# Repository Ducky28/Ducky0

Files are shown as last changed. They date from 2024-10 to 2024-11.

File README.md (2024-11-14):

# Ducky0
A Voron 0.2r1 CoreXY 3D Printer Modification

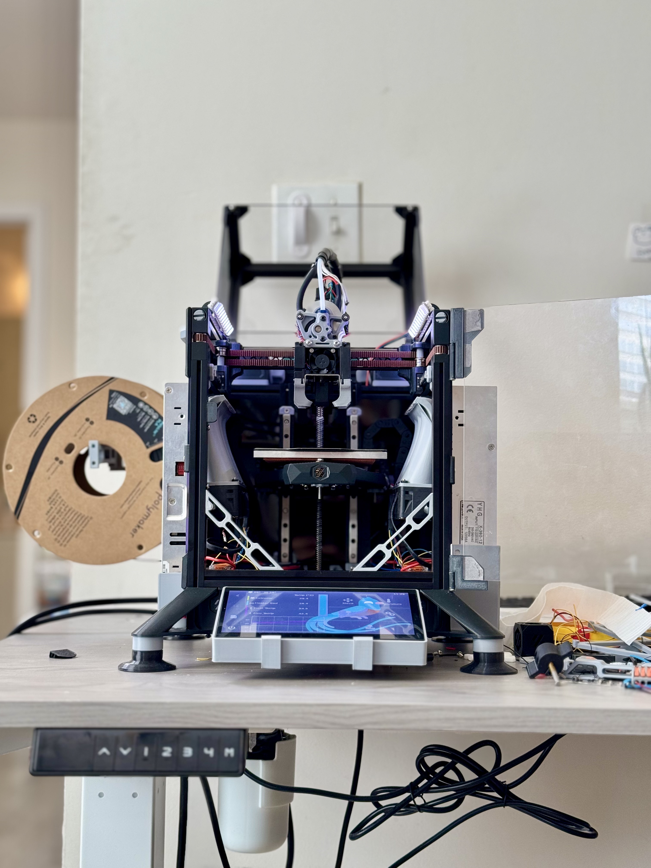
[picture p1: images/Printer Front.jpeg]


## Wait! But Why?
I often find myself in this situation: *sends prototype to 3D printer, 3D printer is done an hour later, realizes I'm on version 7 of the design* 
## Design goals
* Robustness
    * Stiffen up frame where possible
    * Double shear AB motor mounts for higher belt tensions
    * Ultrawide stance feet for added stability
    * Overspecced MCU and Klipper Host to avoid stability issues
* Part cooling
    * 6 4028 Delta fans for sheet cooling
    * 2 4010 blower fans for tool head part cooling
    * Dedicated 12V supply for fans
* Electronics cooling
    * As much cooling as possible for XY and Z motors
    * put heatinks on stepper stators to improve heat transfer to the air
    * Fans for high current and fast switching components (like stepper drivers)
* Extrusion system
    * [Deconstruder tool head](https://github.com/TheRealDeathsneeze/Deconstruder/tree/main)
    * 60-80mm^3/sec volumetric flow rate
    * 0.4mm high flow nozzle
    * Decently high torque extruder
* XYZ motion
    * 100,000mm/sec^2 acceleration
    * 1000mm/sec speed (600-700mm/sec printing speed)
    * Ultra light gantry
    * 5000mm/sec^2 Z acceleration
    * 200mm/sec Z speed
* Power
    * 5V 25W USB-C supply for Raspberry Pi 
    * 12V 350W PSU for fans
    * 24V 350W PSU for main electronics
    * 48V 200W PSU for XY motors
    * Separately switch 48V supply from the rest of the supplies
* Printing Capabilities
  * Fully enclosed with standard tophat and door
  * Fully contained part cooling
  * Copper heatblock for up to 450C
  * Heated bed up to 120C
  * Max observed chamber temperature: 75C

* Must be able to print these materials
     * ABS/ASA
     * PET
     * PA6/PA12
     * PLA
     * PETG
     * PC
   
## Components and Resources
* Frame Components
  * [Voron V0 Frame Brace by Jon](https://www.printables.com/model/450049-voron-v0-frame-brace)
  * [Voron V0 Stealth Handles by Maple Leaf Makers](https://www.printables.com/model/481575-voron-v0-stealth-handles)
  * Extrusions and mounting hardware used in formbot kit
* Tool head and gantry
    * [Deconstruder tool head by Becca Kay](https://github.com/TheRealDeathsneeze/Deconstruder)
    * 4010 12krpm GDSTime fans
    * NF Crazy Copper Volcano High Flow
    * 0.4mm Bondtech Brass CHT nozzle
    * LDO-36STH20-1004AHG(8T) extruder motor
    * PT1000 thermistor
    * 120W heater cartridge
* XY Motion
  * Fysetc Voron 0 ultra light gantry
  * [Double shear AB motor mounts by Driftrotor](https://github.com/Driftrotor/Voron-V0.2r1-Double-Shear-AB-Motor-Mounts/tree/main)
  * LDO-35sth52-2004AH(s35) XY motors
  * 2 3010 fans for stepper cooling
  * 2 3010 blower fans for stepper cooling
  * 2 12032 blower fans for stepper cooling
* Electronics
  * Raspberry pi 4 for Klipper Host
  * BTT SKR 3 for primary Klipper MCU
  * LDO Nitehawk 36 for tool board MCU
  * 2 Mellow Fly TMC5160 Pro drivers for XY motors
  * 2 BTT TMC2209 stepper drivers for Z and E motors
  * 4 4010 fans for electronics cooling
  * Remixed Voron 0.2 printed bottom panel. [original model by Cthulhu](https://www.printables.com/model/467247-voron-02-printed-bottom-panel)
  * [Mellow Fly HV-TMC5160 Pro Driver case by Hundsbuah](https://www.thingiverse.com/thing:5792659)
  * Embedded glass bead thermistors inside AB motors to track motor winding temperature
  * Makerbase MKS 3MOS fan mosfets
* Misc
  * 6 Delta Electronics PFB0412EN-E fans
  * Fysetc CNC bed frame
  * [4028 Air ducts by Coconut](https://github.com/CoconutDevelopment/CocobustorZero/tree/main/STLs/Coconut%20Air%20Ducts)
  * [Superwide Stance feet by Coconut](https://github.com/CoconutDevelopment/CocobustorZero/tree/main/STLs/Superwide%20Stance)
  * BTT Pi TFT70 touchscreen
  * [BTT Pi TFT70 screen enclosure by Fizzy's Tech](https://www.printables.com/model/581227-ft-btt-pi-tft70-screen-mount/files)
  * [Voron 0 Kirigami Bed by christophmuellerorg](https://github.com/christophmuellerorg/voron_0_kirigami_bed)
  * [Rainbow on a Matchstick by Blamm](https://github.com/VoronDesign/Voron-Hardware/tree/master/Daylight/Rainbow_on_a_matchstick)
  * [Lift-Off Tophat Hinges by chirpy2605](https://github.com/chirpy2605/voron/tree/main/V0/Lift-Off_Tophat_Hinges)
  * [Remixed MF Nano carbon filter by kejar31](https://www.printables.com/model/500513-voron-v0-tiny-recirculating-carbon-filter-mfnano-r)

## Short Video
Video (https://www.youtube.com/watch?v=nS1hlO0ZEqE)

## Explainer Video
Video (https://www.youtube.com/watch?v=TwCCUQ7yJMo)

## Benchy!
Video (https://www.youtube.com/watch?v=4r7pd2CCRk0)

## Authors

[@Ducky28](https://github.com/Ducky28)

## Version History

* 0.1.19
     * Added Klipper Expander board for more I/O
     * [Added Remixed MF Nano carbon filter by kejar31](https://www.printables.com/model/500513-voron-v0-tiny-recirculating-carbon-filter-mfnano-r)
     * Added 2 chamber thermistors to monitor chamber temp
     * Separated fan controls for better control over different fans
     * moved pin definitions around to more sensible hardware (no more turning fans on and off with a high power heater mosfet)

* 0.1.01
     * Added Thermistors and thermal adhesive to BOM for embedding thermistors inside motors
     * Added KAMP Smart Park and Adaptive Purge routines in PRINT_START
     * Added Orcaslicer, Prusaslicer, and Cura print profiles for KAMP conditional gcodes
     * Still work in progress, things may still not work as expected!

* 0.1
    * Initial Release
    * Still work in progress, things may not work as expected!
 
## License

This project is licensed under the GPL-V3.0 License - see the LICENSE.md file for details

## Acknowledgments

* [VoronDesign](https://github.com/VoronDesign)
  * [Voron 0.2r1](https://github.com/VoronDesign/Voron-0)
  * [Klipper Expander by Tim Abraham](https://github.com/VoronDesign/Voron-Hardware/tree/master/Klipper_Expander/Documentation)
* [Klipper3D Klipper](https://github.com/Klipper3d/klipper)
  * [Klippain Shaketune by Frix-x](https://github.com/Frix-x/klippain-shaketune)
  * [Klipper TMC Autotune by Andrew McGregor](https://github.com/andrewmcgr/klipper_tmc_autotune)
  * [Klipperscreen by Jordan Ruthe](https://github.com/KlipperScreen/KlipperScreen)
  * [KAMP by kyleisah](https://github.com/kyleisah/Klipper-Adaptive-Meshing-Purging)
* [Coconut](https://github.com/CoconutDevelopment)
  * [CocobustorZero](https://github.com/CoconutDevelopment/CocobustorZero)
* [247 printing's 247 Zero Beta2](https://github.com/247printing/247zero)
* [Stefan's (CNC Kitchen) "Fast 3D printing is bad for Strength! (and how to fix it!)" video](https://youtu.be/qBvTWFEd7rk?si=yeHNLQK2HN_pLwcw) (Inspiration)
* [Vez3D VzBoT](https://github.com/VzBoT3D/VzBoT-Vz330) (Inspiration)
* All the people that have took their precious time to look at what I made and provide feedback and resources to get the project to where it is now and all the things I have learned along the way! Thank you!

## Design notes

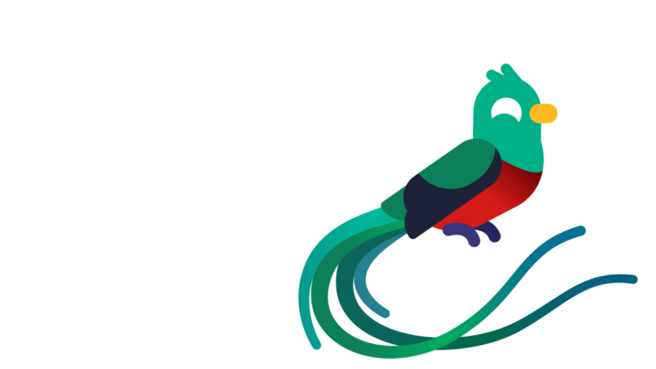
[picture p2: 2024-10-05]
firmwares/duckytheme/images/background.png

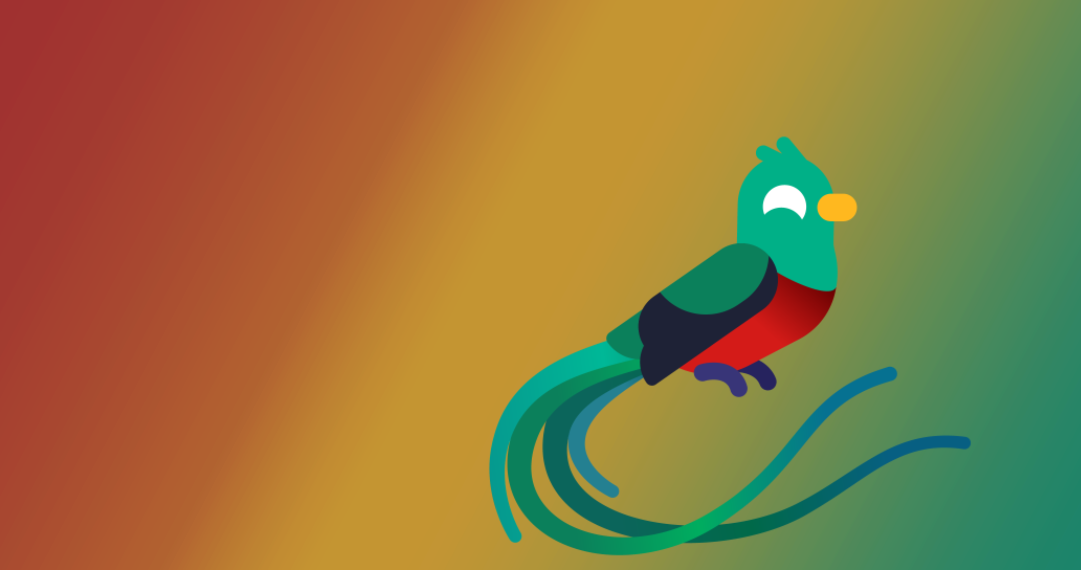
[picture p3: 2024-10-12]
firmwares/.fluidd-theme/background.png

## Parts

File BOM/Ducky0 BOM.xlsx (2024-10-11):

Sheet: Cover
THIS BOM CONTAINS ALL HARDWARE IN ADDITION TO THE STANDARD VORON 0.2r1 BOM! THIS BOM IS PROVIDED AS IS AND IS STILL A WORK IN PROGRESS! SO THINGS MIGHT BE MISSING OR NOT ACCOUNTD FOR IN THIS BOM!

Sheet: Hardware
Hardware
Qty | Component
25 | M3x6 BCHS
18 | M3x8 BCHS
45 | M3 Hexnut
36 | M3x40 BCHS
10 | 40x40x11mm heatsinks | Note: Do not buy the ones with adhesive backings on them, they have a very poor contact patch with the stepper motor making them ineffective at their job, I would highly recommend bodning them to the stepper motor with thermal glue.

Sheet: Electronics
Electronics
Qty | Component | Part No. | Source | Link
1 | BTT SKR 3 | 1020000418 | BIQU | https://biqu.equipment/products/bigtreetech-btt-skr-3-control-board-for-3d-printer
1 | BTT Pi TFT70 V2.1 | 1040000044 | BIQU | https://biqu.equipment/products/bigtreetech-pi-tft43-v2-0-screen-board?variant=39337700851810
1 | 1m Screen Ribbon cable |  | DIYzone | https://www.aliexpress.us/item/2251832659066152.html
1 | Meanwell LRS-350-24 | 1866-3346-ND | Digikey | https://www.digikey.com/en/products/detail/mean-well-usa-inc/LRS-350-24/7705034
1 | Meanwell LRS-350-12 | 1866-3344-ND | Digikey | https://www.digikey.com/en/products/detail/mean-well-usa-inc/LRS-350-12/7705030
1 | Meanwell UHP-200-48 | 1866-4957-ND | Digikey | https://www.digikey.com/en/products/detail/mean-well-usa-inc/UHP-200-48/7707242
6 | Delta PFB0412EN-E | 603-PFB0412EN-E-ND | Digikey | https://www.digikey.com/en/products/detail/delta-electronics/PFB0412EN-E/13912233
5 | GDSTime 4010 fans | GDT4010S12B | GDSTime | https://www.aliexpress.us/item/2251832542216467.html
2 | GDSTime 1232 Blowers | GDB1232 | GDSTime | https://www.aliexpress.us/item/2251832457472831.html
1 | LDO Nitehawk 36 | NH-36 | LDO Motors | https://west3d.com/products/nitehawk-36-usb-toolboard-pcb-by-ldo-motors
2 | Mellow Fly TMC 5160 Pro V1.5 | 5061017165 | Mellow 3D | https://www.aliexpress.us/item/3256804043118800.html
1 | BTT TMC 2209 V1.3 | 1040000053 | BIQU | https://biqu.equipment/products/bigtreetech-tmc2209-stepper-motor-driver-for-3d-printer-board-vs-tmc2208
1 | WAGO 221 Lever Nut set | B0BN6MBR7X | Peppy Producs | https://www.amazon.com/Compact-Splicing-Connector-Assortment-221-2401/dp/B0BN6MBR7X
2 | LDO-35sth52-2004(s35) |  | Fabreeko | https://www.fabreeko.com/products/ldo-motors-ldo-35sth52-2004s35
1 | LDO-36STH20-1004AHG(8T) |  | Luke's Lab | https://lukeslabonline.com/products/ldo-36sth20-1004ahg8t-36mm-pancake-stepper-motor
2 | GDSTime 4010 Blowers | GDB4010 | GDSTime | https://www.aliexpress.us/item/3256804907966353.html
2 | Rainbow on a Matchstick |  | West3D | https://west3d.com/products/rainbow-on-a-matchstick
1 | USB Hub | H302S | SmartQ | https://www.amazon.com/SmartQ-Expander-Transfer-Splitter-Compatible/dp/B09PTVSMLB
2 | NTC 3950 Thermistor | B0CL4D5QB8 | TIEXYE | https://www.amazon.com/Thermistor-Printer-Sensor-Creality-Voxelab/dp/B0CL4D5QB8
1 | G109 Thermal Glue | B072MSXHJD | GENNEL | https://www.amazon.com/GENNEL-Conductive-Silicone-Adhesive-Compound/dp/B072MSXHJD

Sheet: Tool head
Tool Head
Qty | Component | Part No. | Source | Link
1 | NF Crazy Volcano HF |  | Mellow 3D | ???
1 | Delta ASB02505SHA-AY6B | 603-2080-ND | Digikey | https://www.digikey.com/en/products/detail/delta-electronics/asb02505sha-ay6b/7491489
1 | Bondtech CHT Volcano 0.4mm | 600-C-CHT-VOL-175-40 | Bondtech | https://www.bondtech.se/product/bondtech-cht-volcano-coated-brass-nozzle/
1 | 100W 24V 6x20mm heater cartridge |  | Luke's Lab | https://lukeslabonline.com/products/high-wattage-heater?variant=47315067273517
1 | RTD-PT1000 Thermistor |  | Slice Engineering | https://www.sliceengineering.com/products/rtd-pt1000

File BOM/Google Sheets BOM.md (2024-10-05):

Google sheets Link: https://docs.google.com/spreadsheets/d/1ZFCBsGUMRQd7YihfarKY5RAe8jz7l1DWx4ru8DRhnw0/edit?usp=sharing

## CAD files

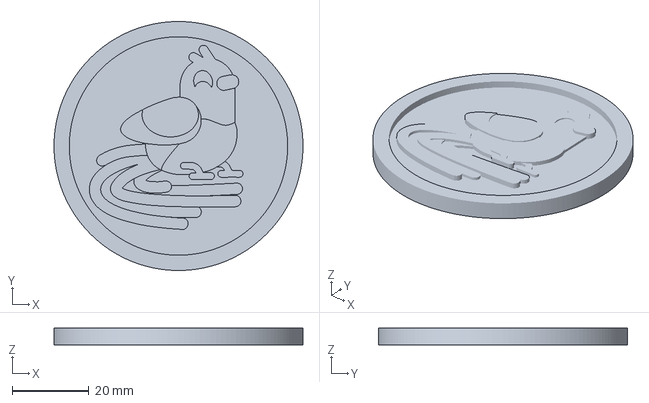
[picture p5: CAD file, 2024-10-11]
Profiles/Ducky0StarterProfileOrcaslicer.3mf
65.0 x 65.0 x 4.39 mm

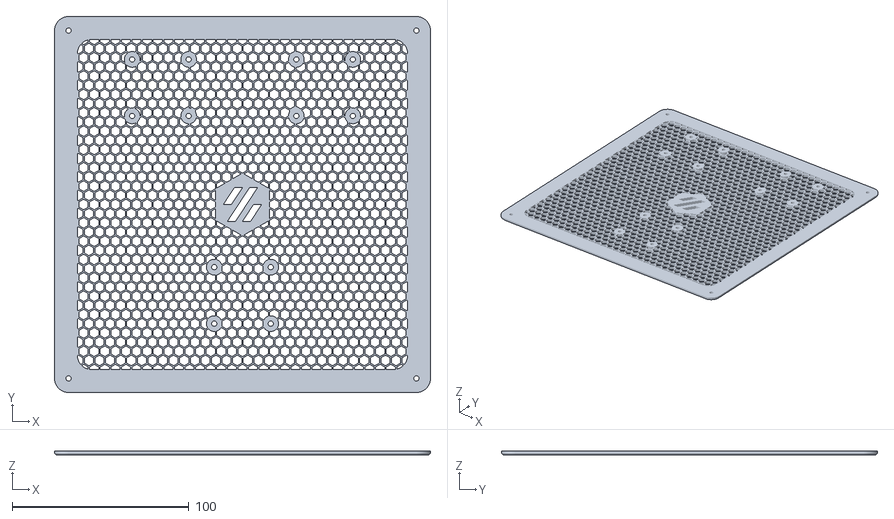
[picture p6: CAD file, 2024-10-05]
STLs/v0.2 bottom panel.stl
213.0 x 213.0 x 2.40

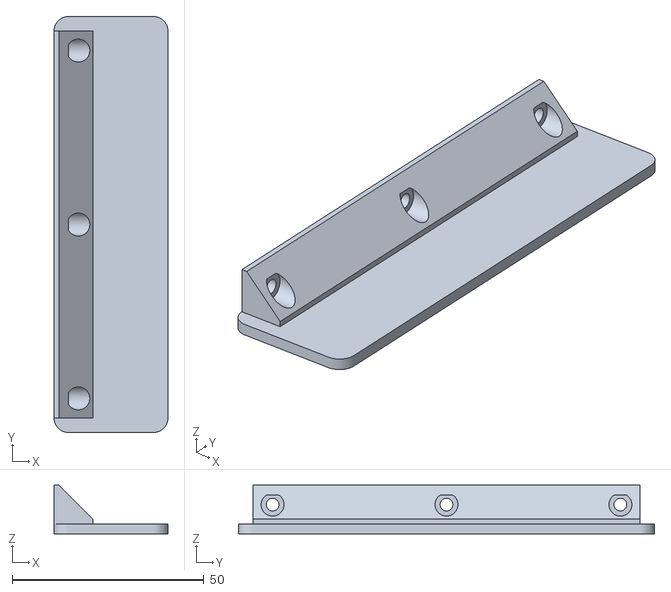
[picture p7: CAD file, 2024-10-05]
STLs/USB Hub Mount.stl
29.7 x 108.5 x 12.7

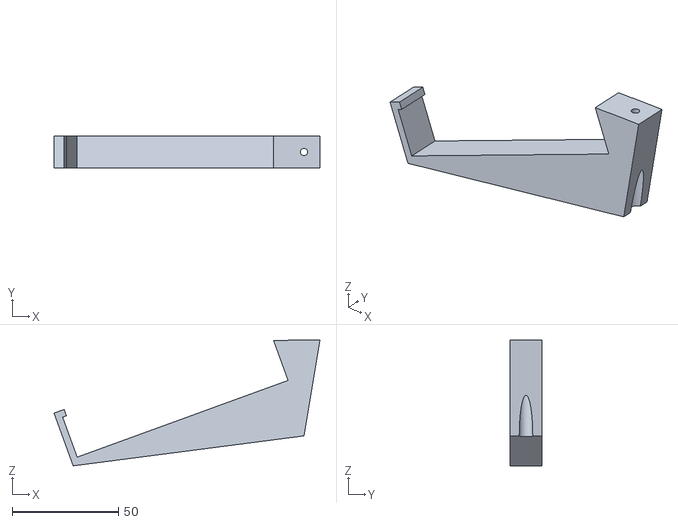
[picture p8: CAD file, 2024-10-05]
STLs/FT BTT Pi TFT70 Screen enclosure mount.stl
125.0 x 15.0 x 59.0

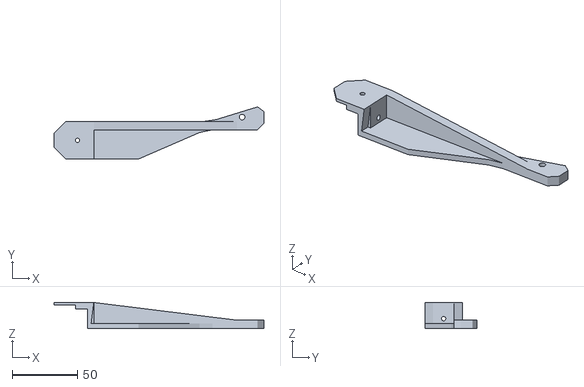
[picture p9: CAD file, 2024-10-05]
STLs/12032 Motor cooling bracket top left.stl
160.4 x 39.9 x 19.9

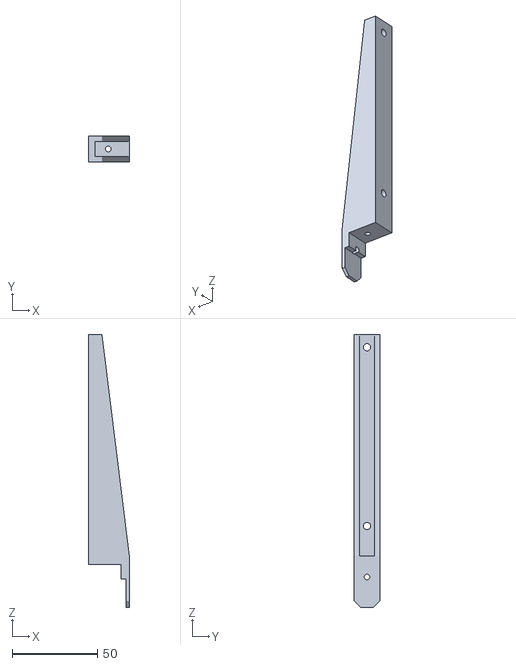
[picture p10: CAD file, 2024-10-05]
STLs/12032 motor cooling bracket.stl
23.9 x 15.0 x 160.4

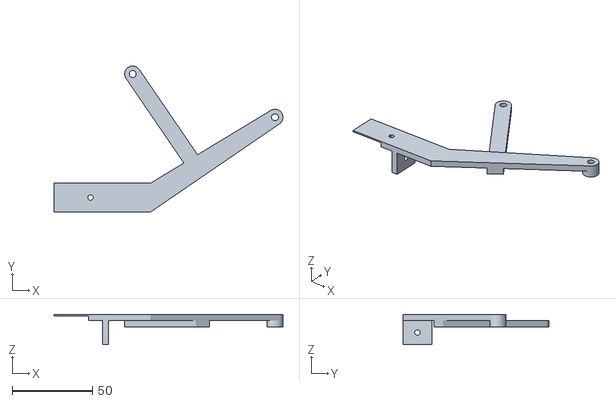
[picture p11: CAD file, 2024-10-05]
STLs/12032 motor cooling bracket bottom left.stl
143.1 x 91.2 x 18.8

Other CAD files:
Profiles/Ducky0StarterProfileCura.3mf
STLs/12032 motor cooling top bracket.stl

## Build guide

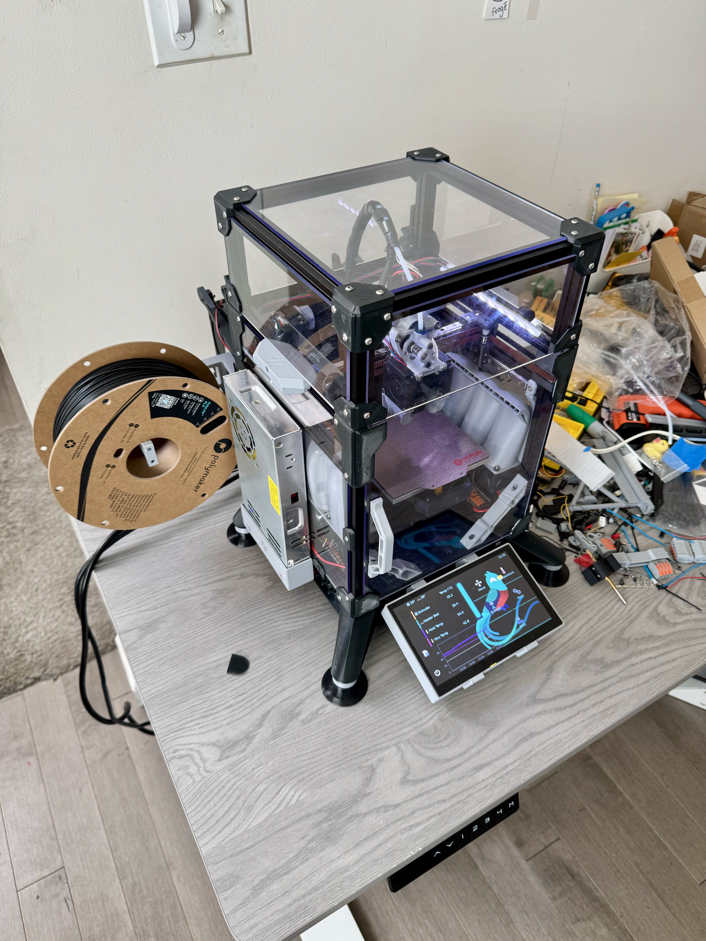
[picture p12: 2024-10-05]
images/Printer Left 3:4 view.jpeg

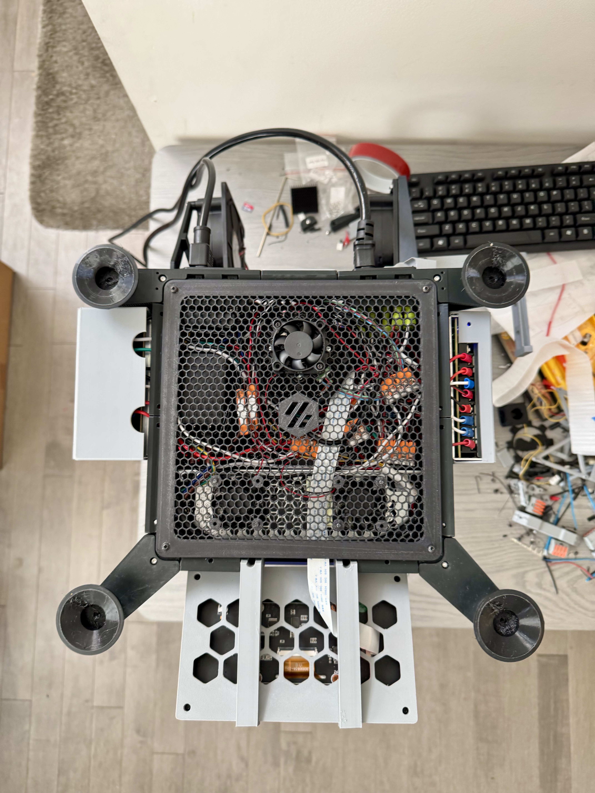
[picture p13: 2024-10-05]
images/Printer Bottom Electronics.jpeg

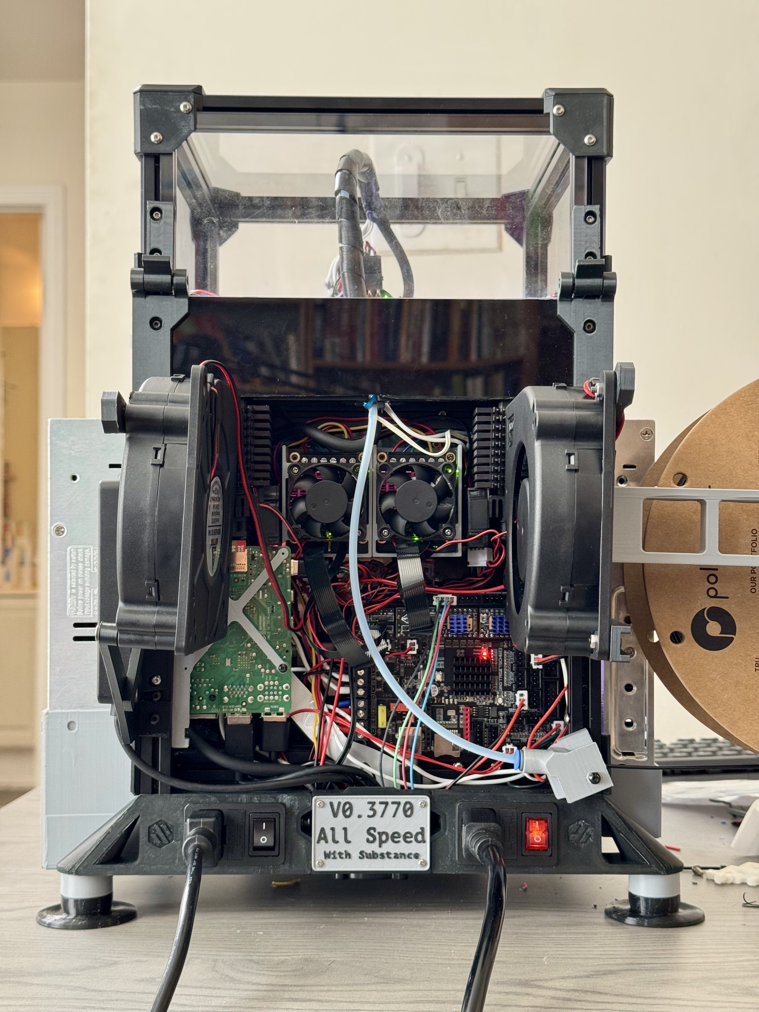
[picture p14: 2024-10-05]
images/Printer Rear Electronics.jpeg

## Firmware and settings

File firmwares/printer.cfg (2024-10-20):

[include fluidd.cfg]
[virtual_sdcard]
path: /home/pi/printer_data/gcodes
on_error_gcode: CANCEL_PRINT

# This file contains common pin mappings for the BigTreeTech SKR 3.
# To use this config, the firmware should be compiled for the
# STM32H743 with a "128KiB bootloader".

# See docs/Config_Reference.md for a description of parameters.

[include mainsail.cfg]
# This file contains common pin mappings for the BIGTREETECH SKR3
# To use this config, the firmware should be compiled for the
#[*] Enable extra low-level configuration options
#Micro-controller Architecture = STMicroelectronics STM32
#Processor model = STM32H723
#Bootloader offset = (128KiB bootloader (SKR SE BX v2.0))
#Clock Reference = 25 MHz crystal
#Communication interface = USB (on PA11/PA12)

# The "make flash" command does not work on the SKR3. Instead,
# after running "make", copy the generated "out/klipper.bin" file to a
# file named "firmware.bin" on an SD card and then restart the SKR3
# with that SD card.

## *** THINGS TO CHANGE/CHECK: ***
## MCU path                                                                     [mcu] section
## Z and Extruder motor currents                                                [tmc2209 stepper_*] sections. Uncomment the stepper motor you have
## Full steps per rotation for Extruder                                         [extruder] section
## Thermistor types                                                             [extruder] and [heater_bed] sections - See https://www.klipper3d.org/Config_Reference.html#common-thermistors for common thermistor types
## Motor currents                                                               [extruder] [stepper] and [_HOME_X/Y] macro sections
## PID tune                                                                     [extruder] and [heater_bed] sections
## Fine tune E steps                                                            [extruder] section
## For more info                                                                check https://docs.vorondesign.com/build/startup/#v0

[mcu]
#####################################################################
# Obtain definition by "ls -l /dev/serial/by-id/"
#####################################################################
serial: /dev/serial/by-id/usb-Klipper_stm32h723xx_2E0025000851313332323730-if00

[mcu nhk]
##  Obtain definition by "ls -l /dev/serial/by-id/" then unplug to verify
##--------------------------------------------------------------------
serial: /dev/serial/by-id/usb-Klipper_rp2040_303339383409635B-if00
restart_method: command
##--------------------------------------------------------------------

[mcu expander]
serial: /dev/serial/by-id/usb-Klipper_stm32f042x6_220024000843565036343620-if00
restart_method: command

[temperature_sensor mcu_temp]
sensor_type: temperature_mcu
min_temp: 0
max_temp: 100

[temperature_sensor host_temp]
sensor_type: temperature_host
min_temp: 10
max_temp: 100

[printer]
kinematics: corexy
max_velocity: 1000
max_accel: 120000
max_z_velocity: 180
max_z_accel: 5000
square_corner_velocity: 120
minimum_cruise_ratio: 0.0

[stepper_y]
step_pin: PD4
dir_pin: !PD3
enable_pin: !PD6
microsteps: 32
rotation_distance: 40
full_steps_per_rotation: 200    
endstop_pin: tmc5160_stepper_x:virtual_endstop
position_endstop: 120
position_max: 120
homing_speed: 80
homing_retract_dist: 0
homing_positive_dir: True

[tmc5160 stepper_y]
cs_pin: PD5
#spi_bus: spi1
spi_software_miso_pin: PE15
spi_software_mosi_pin: PE13
spi_software_sclk_pin: PE14
run_current: 2.5
interpolate: True
sense_resistor: 0.033
driver_SGT: 1
stealthchop_threshold: 0
diag0_pin: ^!PC1

[stepper_x]
step_pin: PA15
dir_pin: !PA8
enable_pin: !PD1
microsteps: 32
rotation_distance: 40
full_steps_per_rotation: 200    
endstop_pin: tmc5160_stepper_y:virtual_endstop
position_endstop: 120
position_max: 120
homing_speed: 80
homing_retract_dist: 0
homing_positive_dir: True

[tmc5160 stepper_x]
cs_pin: PD0
#spi_bus: spi2
spi_software_miso_pin: PE15
spi_software_mosi_pin: PE13
spi_software_sclk_pin: PE14
run_current: 2.5
interpolate: True
sense_resistor: 0.033
driver_SGT: 1
stealthchop_threshold: 0
diag0_pin: ^!PC3

[stepper_z]
step_pin: PE2
dir_pin: PE3
enable_pin: !PE0
microsteps: 32
rotation_distance: 8
endstop_pin: ^PC0
#position_endstop: 120
position_max: 110
position_min: -1.5
homing_speed: 50
second_homing_speed: 3.0
homing_retract_dist: 5.0

[tmc2209 stepper_z]
uart_pin: PE1
run_current: 0.7
#uart_address: 1
#diag_pin:
sense_resistor: 0.110
interpolate: True
stealthchop_threshold: 0

[extruder]
step_pin: nhk:gpio23
dir_pin: nhk:gpio24
enable_pin: !nhk:gpio25
gear_ratio: 50:8    
microsteps: 128
rotation_distance: 21.384
nozzle_diameter: 0.600
filament_diameter: 1.750
heater_pin: PB3
sensor_type: PT1000
sensor_pin: nhk:gpio29
pullup_resistor: 2200
#control = pid
#pid_kp = 18.663
#pid_ki = 0.943
#pid_kd = 92.384
min_temp: 0
min_extrude_temp: 0
max_temp: 400
max_extrude_only_distance: 200
max_extrude_cross_section: 8
pressure_advance_smooth_time: 0.020

[tmc2209 extruder]
sense_resistor: 0.100
uart_pin: nhk:gpio0
tx_pin: nhk:gpio1
run_current: 0.85
interpolate: False
stealthchop_threshold: 0    

#[extruder1]
#step_pin: PD11
#dir_pin: PD10
#enable_pin: !PD13
#heater_pin: PB4
#sensor_pin: PA3
#...

[temperature_sensor a_motor]
sensor_type: Generic 3950
sensor_pin: PA2
min_temp: 0
max_temp: 180
#   See the "extruder" section for the definition of the above
#   parameters.
#gcode_id:
#   See the "heater_generic" section for the definition of this
#   parameter.
[temperature_sensor b_motor]
sensor_type: Generic 3950
sensor_pin: PA3
min_temp: 0
max_temp: 180
#   See the "extruder" section for the definition of the above
#   parameters.
#gcode_id:
#   See the "heater_generic" section for the definition of this
#   parameter.

[temperature_sensor chamber]
sensor_type: Generic 3950
sensor_pin: expander:PA6
min_temp: 0
max_temp: 80
#   See the "extruder" section for the definition of the above
#   parameters.
#gcode_id:
#   See the "heater_generic" section for the definition of this
#   parameter.

[temperature_sensor chamber_bottom]
sensor_type: Generic 3950
sensor_pin: expander:PA5
min_temp: 0
max_temp: 80
#   See the "extruder" section for the definition of the above
#   parameters.
#gcode_id:
#   See the "heater_generic" section for the definition of this
#   parameter.

[temperature_sensor chamber]
sensor_type: Generic 3950
sensor_pin: expander:PA6
min_temp: 0
max_temp: 180
#   See the "extruder" section for the definition of the above
#   parameters.
#gcode_id:
#   See the "heater_generic" section for the definition of this
#   parameter.

[heater_bed]
heater_pin: PD7
sensor_type: Generic 3950
sensor_pin: PA1
control = pid
pid_kp = 57.640
pid_ki = 2.448
pid_kd = 339.358
min_temp: 0
max_temp: 120

#[output_pin big_fan_power]
#pin: PB4
#value: 1
#shutdown_value: 0 #turn big fan power off when MCU is shut down

[fan_generic fan2]
pin: !PB7
shutdown_speed: 0
cycle_time: 0.00004
enable_pin: expander:PA1
off_below: 0.06
hardware_pwm: false

[controller_fan fan_0]
pin: PB6
cycle_time: 0.005
fan_speed: 1.0
idle_speed: 0.35
shutdown_speed: 0
#heater: none
stepper: stepper_x, stepper_y

[fan_generic fan3]
pin: !expander:PA2
cycle_time: 0.00004
shutdown_speed: 0
off_below: 0.12
enable_pin: expander:PA3
hardware_pwm: false

[fan_generic fan0]
pin: nhk:gpio6
cycle_time: 0.005
shutdown_speed: 0
off_below: 0.06
kick_start_time: 0.100


[heater_fan hotend_fan]
pin: nhk:gpio5
tachometer_pin: nhk:gpio16
tachometer_ppr: 2
tachometer_poll_interval: 0.0009

[controller_fan big_motor_fan]
pin: expander:PA0
cycle_time: 0.02
fan_speed: 1.0
idle_speed: 0.1
kick_start_time: 0.500
shutdown_speed: 0
stepper: stepper_x, stepper_y

[controller_fan z_motor_fan]
pin: PB5
cycle_time: 0.02
fan_speed: 1.0
idle_speed: 0.1
kick_start_time: 0.500
shutdown_speed: 0
stepper: stepper_z

#####################################################################
#   Accelerometer
#####################################################################
[adxl345]
cs_pin: nhk:gpio27
spi_software_sclk_pin: nhk:gpio18
spi_software_mosi_pin: nhk:gpio20
spi_software_miso_pin: nhk:gpio19

[resonance_tester]
probe_points: 
    60, 60, 30
accel_chip: adxl345
min_freq: 5
max_freq: 200
accel_per_hz: 75

[input_shaper]
shaper_freq_x: 93.0
shaper_freq_y: 80.4
shaper_type_x: mzv
shaper_type_y: mzv
damping_ratio_x: 0.037
damping_ratio_y: 0.04

[exclude_object]

#####################################################################
# Neopixel stuff
#####################################################################

[neopixel chamber_led]
pin: PE6
chain_count: 20
color_order: GRB
initial_RED: 0.5
initial_GREEN: 0.5
initial_BLUE: 0.4
initial_WHITE: 0.0
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

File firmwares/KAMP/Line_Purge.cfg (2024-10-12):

[gcode_macro LINE_PURGE]
description: A purge macro that adapts to be near your actual printed objects
gcode:
    # Get relevant printer params
    {% set travel_speed = (printer.toolhead.max_velocity) * 60 | float %}
    {% set cross_section = printer.configfile.settings.extruder.max_extrude_cross_section | float %}
    
    # Use firmware retraction if it is defined
    {% if printer.firmware_retraction is defined %}
        {% set RETRACT = G10 | string %}
        {% set UNRETRACT = G11 | string %}
    {% else %}
        {% set RETRACT = 'G1 E-.5 F2100' | string %}
        {% set UNRETRACT = 'G1 E.5 F2100' | string %}
    {% endif %}

    # Get purge settings from _Kamp_Settings
    {% set verbose_enable = printer["gcode_macro _KAMP_Settings"].verbose_enable | abs %}
    {% set purge_height = printer["gcode_macro _KAMP_Settings"].purge_height | float %}
    {% set tip_distance = printer["gcode_macro _KAMP_Settings"].tip_distance | float %}
    {% set purge_margin = printer["gcode_macro _KAMP_Settings"].purge_margin | float %}
    {% set purge_amount = printer["gcode_macro _KAMP_Settings"].purge_amount | float %}
    {% set flow_rate = printer["gcode_macro _KAMP_Settings"].flow_rate | float %}


    # Calculate purge origins and centers from objects
    {% set all_points = printer.exclude_object.objects | map(attribute='polygon') | sum(start=[]) %}    # Get all object points
    {% set purge_x_min = (all_points | map(attribute=0) | min | default(0)) %}                          # Object x min
    {% set purge_x_max = (all_points | map(attribute=0) | max | default(0)) %}                          # Object x max
    {% set purge_y_min = (all_points | map(attribute=1) | min | default(0)) %}                          # Object y min
    {% set purge_y_max = (all_points | map(attribute=1) | max | default(0)) %}                          # Object y max

    {% set purge_x_center = ([((purge_x_max + purge_x_min) / 2) - (purge_amount / 2), 0] | max) %}      # Create center point of purge line relative to print on X axis
    {% set purge_y_center = ([((purge_y_max + purge_y_min) / 2) - (purge_amount / 2), 0] | max) %}      # Create center point of purge line relative to print on Y axis

    {% set purge_x_origin = ([purge_x_min - purge_margin, 0] | max) %}                                  # Add margin to x min, compare to 0, and choose the larger
    {% set purge_y_origin = ([purge_y_min - purge_margin, 0] | max) %}                                  # Add margin to y min, compare to 0, and choose the larger

    # Calculate purge speed
    {% set purge_move_speed = (flow_rate / 5.0) * 60 | float %}

    {% if cross_section < 5 %}

        {action_respond_info("[Extruder] max_extrude_cross_section is insufficient for purge, please set it to 5 or greater. Purge skipped.")}

    {% else %}

        {% if verbose_enable == True %}

        {action_respond_info("Moving filament tip {}mms".format(                                                                 
            (tip_distance),                                                                                      
        )) }
        {% endif %}

        {% if printer.firmware_retraction is defined %}
            {action_respond_info("KAMP purge is using firmware retraction.")}
        {% else %}
            {action_respond_info("KAMP purge is not using firmware retraction, it is recommended to configure it.")}
        {% endif %}

        {% if purge_y_origin > 0 %}
        
            {action_respond_info("KAMP purge starting at {}, {} and purging {}mm of filament, requested flow rate is {}mm3/s.".format(                                                                 
                (purge_x_center),
                (purge_y_origin),
                (purge_amount),
                (flow_rate),
            )) }
    
        {% else %}
    
            {action_respond_info("KAMP purge starting at {}, {} and purging {}mm of filament, requested flow rate is {}mm3/s.".format(                                                                 
                (purge_x_origin),
                (purge_y_center),
                (purge_amount),
                (flow_rate),
            )) }

        {% endif %}

        SAVE_GCODE_STATE NAME=Prepurge_State                                                    # Create gcode state

        {% if purge_y_origin > 0 %}                                                             # If there's room on Y, purge along X axis in front of print area

            G92 E0                                                                              # Reset extruder
            G0 F15000                                                                           # Set travel speed
            G90                                                                                 # Absolute positioning
            G0 X{purge_x_center} Y{purge_y_origin} F15000                                       # Move to purge position
            G0 Z{purge_height} F3000                                                            # Move to purge Z height
            M83                                                                                 # Relative extrusion mode
            G1 E{tip_distance} F{purge_move_speed}                                              # Move filament tip
            G1 X{purge_x_center + purge_amount} E{purge_amount} F{purge_move_speed}             # Purge line
            {RETRACT}                                                                           # Retract
            G0 X{purge_x_center + purge_amount + 10} F15000                                     # Rapid move to break string
            G92 E0                                                                              # Reset extruder distance
            M82                                                                                 # Absolute extrusion mode
            G0 Z{purge_height * 2} F3000                                                        # Z hop

        {% else %}                                                                              # If there's room on X, purge along Y axis to the left of print area
            
            G92 E0                                                                              # Reset extruder
            G0 F15000                                                                           # Set travel speed
            G90                                                                                 # Absolute positioning
            G0 X{purge_x_origin} Y{purge_y_center} F15000                                       # Move to purge position
            G0 Z{purge_height} F3000                                                            # Move to purge Z height
            M83                                                                                 # Relative extrusion mode
            G1 E{tip_distance} F{purge_move_speed}                                              # Move filament tip
            G1 Y{purge_y_center + purge_amount} E{purge_amount} F{purge_move_speed}             # Purge line
            {RETRACT}                                                                           # Retract
            G0 Y{purge_y_center + purge_amount + 10} F15000                                     # Rapid move to break string
            G92 E0                                                                              # Reset extruder distance
            M82                                                                                 # Absolute extrusion mode
            G0 Z{purge_height * 2} F3000                                                        # Z hop

        {% endif %}

        RESTORE_GCODE_STATE NAME=Prepurge_State                                                 # Restore gcode state
    
    {% endif %}

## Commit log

2024-10-05 added printer.cfg
    [printer (1).cfg]
2024-10-05 Rename printer (1).cfg to firmwares/printer (1).cfg
    [printer (1).cfg]
2024-10-05 klipperscreen theming
2024-10-05 12032 fan mount initial upload
    [Part Studio 2.stl]
2024-10-05 Rename Part Studio 2.stl to STLs/Part Studio 2.stl
    [Part Studio 2.stl]
2024-10-05 FT BTT Pi TFT70 V0 screen mount added
    [Part Studio 2.stl]
2024-10-05 USB hub mount added
    [Part Studio 1 (1).stl]
2024-10-05 Rename Part Studio 1 (1).stl to USB Hub Mount
2024-10-05 Rename USB Hub Mount to USB Hub Mount.stl
    [USB Hub Mount.stl]
2024-10-05 Rename Part Studio 2.stl to FT BTT Pi TFT70 Screen enclosure mount.stl
    [FT BTT Pi TFT70 Screen enclosure mount.stl]
2024-10-05 Rename Part Studio 1 Copy 1.stl to 12032 motor cooling bracket.stl
    [12032 motor cooling bracket.stl]
2024-10-05 Rename Part Studio 1 Copy 2.stl to 12032 motor cooling top bracket.stl
    [12032 motor cooling top bracket.stl]
2024-10-05 Rename Part Studio 2.stl to 12032 motor cooling bracket bottom left.stl
    [12032 motor cooling bracket bottom left.stl]
2024-10-05 Rename printer (1).cfg to printer.cfg
    [printer.cfg]
2024-10-05 Rename IMG_9070.jpeg to Printer Front.jpeg
2024-10-05 Rename IMG_9071.jpeg to Printer Front enclosed.jpeg
2024-10-05 Rename IMG_9072.jpeg to Printer Left.jpeg
2024-10-05 Rename IMG_9073.jpeg to Printer rear.jpeg
2024-10-05 Rename IMG_9074.jpeg to Printer Rear Electronics.jpeg
2024-10-05 Rename IMG_9075.jpeg to Printer Bottom electronics.jpeg
2024-10-05 Added BOM Excel sheet
    [Ducky0 BOM.xlsx]
2024-10-05 Rename Ducky0 BOM.xlsx to BOM/Ducky0 BOM.xlsx
    [Ducky0 BOM.xlsx]
2024-10-05 Create Google Sheets BOM.md
2024-10-05 Updated BOM
    [Ducky0 BOM (1).xlsx]
2024-10-05 Rename Ducky0 BOM (1).xlsx to Ducky0 BOM.xlsx
    [Ducky0 BOM.xlsx]
2024-10-05 Added V0.2 Remixed Bottom Panel
    [v0.2 bottom panel.stl]
2024-10-05 Added top left 12032 fan mount
    [Part Studio 1 Copy 2 Copy 1 mirrored.stl]
2024-10-05 Rename STLs/Part Studio 1 Copy 2 Copy 1 mirrored.stl to 12032 Motor cooling bracket top left.stl
    [12032 Motor cooling bracket top left.stl]
2024-10-05 Rename 12032 Motor cooling bracket top left.stl to STLs/12032 Motor cooling bracket top left.stl
    [12032 Motor cooling bracket top left.stl]
2024-10-06 Update BOM
    [Ducky0 BOM.xlsx]
2024-10-06 Update printer.cfg to reflect current configuration
    [printer.cfg]
2024-10-11 Adding profiles
    [Ducky0StarterProfileOrcaslicer.3mf]
2024-10-11 Updated Orcalsicer Profile
    [Ducky0StarterProfileOrcaslicer.3mf]
2024-10-12 Added modified KAMP macros
    Added to go a little less ham with the travel moves that it takes from the machine limits
    [Line_Purge.cfg, Smart_Park.cfg]
2024-10-20 Update printer.cfg to include Klipper expander
    [printer.cfg]
